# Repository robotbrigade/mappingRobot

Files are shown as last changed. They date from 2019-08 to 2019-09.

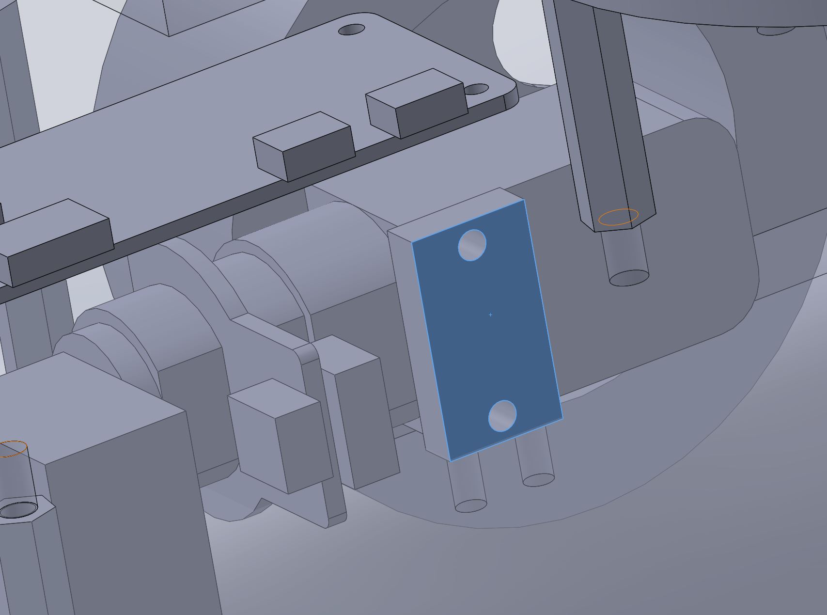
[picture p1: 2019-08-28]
CAD/Reference images/motor mount.jpg

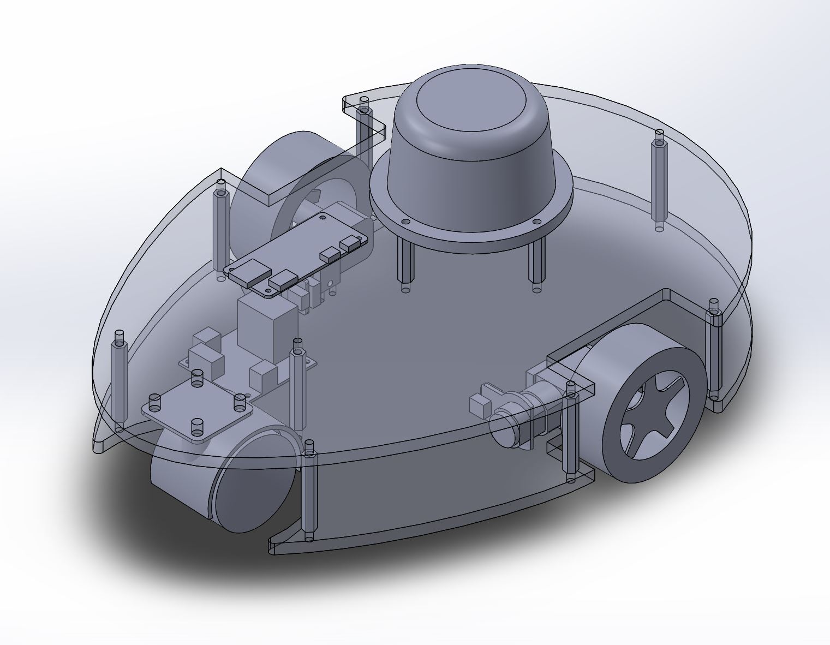
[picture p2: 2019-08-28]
CAD/Reference images/robot-with_transparency.jpg

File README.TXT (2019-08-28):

This readme was last updated on August 8th 2019

This repository will contain all of the files necessary to make a mapping robot that can map its 
environment using a 2D lidar-like sensor.  At the time of writing this README, the project is 
ongoing.  Eventual goals of this project are:

* Have the robot autonomously map its environment using a RPlidar A2 module.   
* Do so using ROS.  
* Run exclusively my own code.
* Be able to connect to the robot using a remote computer which can view the current stat of the
map as well as to take direct control of the robot.  

The robot system will consist of three processors.  The first is the remote computer which does no 
major computation.  The second is an onboard processor that will do the heavy lifting and which holds 
the most up-to-date map.  The third is a low-power processor (currently an arduino) that drives the 
motors, monitors the battery state, and turns on/off the power to the motors, the main processor, and
itself.  

Power is supplied to the robot from an off-the-shelf battery pack for a cordless drill.

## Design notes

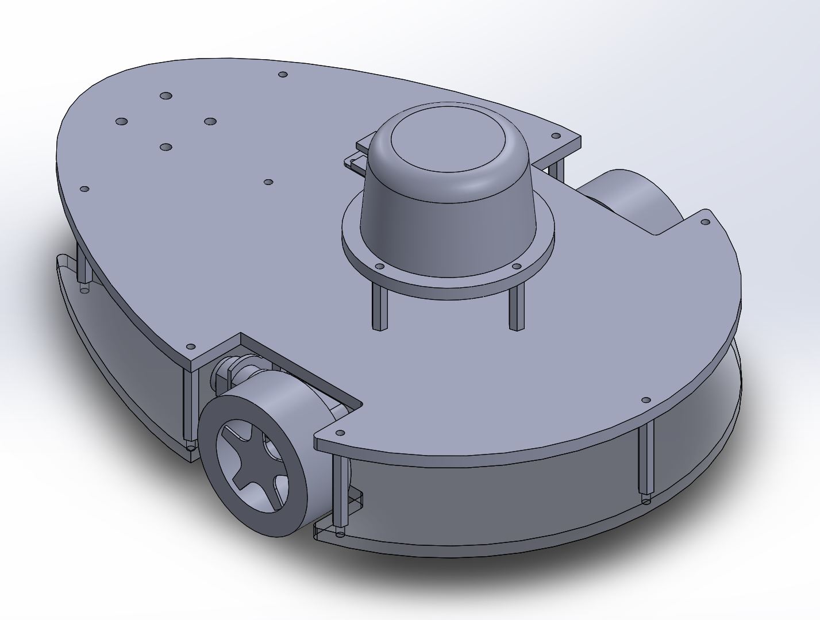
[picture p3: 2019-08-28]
CAD/Reference images/robot-everything_opaque.jpg

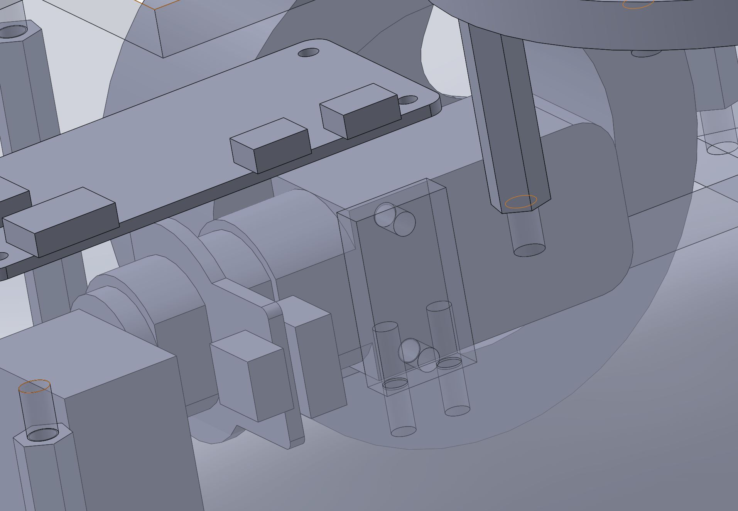
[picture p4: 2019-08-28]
CAD/Reference images/motor-mount-with-transparency.jpg

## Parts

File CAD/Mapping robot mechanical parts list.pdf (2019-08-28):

Quantity | Description | part number | Where to order | Alternate order location | Notes
2 Encoder/motor/gearbox combo | TT Motor with Encoder (6V 160RPM 120:1) | https://www.dfrobot.com/product-1457.html?search=TT%20Motor%20with%20Encoder%20%286V%20160RPM%20120%3A1%29
2 Wheels | https://www.dfrobot.com/product-352.html
1 1/4" black acrylic | https://www.amazon.com/gp/product/B01DYSTH3K
8 1 5/8" standoffs | https://www.mcmaster.com/91115A564
4 1" standoffs | https://www.mcmaster.com/91115A133
28 6-32 machine screws | https://www.mcmaster.com/92949A149
4 M3 machine screws | https://www.mcmaster.com/92000A120
4 6-32 lock nuts | https://www.mcmaster.com/91831A007
1 Caster | https://www.amazon.com/gp/product/B010SLSK48
2 motor mounts | https://www.pololu.com/product/2670https://www.robotshop.com/en/solarbotics-gmb39-gear-motor-bracket.html I scavenged my motor mounts from another project. Here are two mounts that I think would work but which aren't like the ones that I am using. You will need to adjust your CAD files to have the mounting holes be in the right places.
4 motor mount screws | Choose these to work with your motor mount
4 motor mount long machine screws | Choose these to work with your motor mount
4 motor mount lock nuts | Choose these to work with your motor mount

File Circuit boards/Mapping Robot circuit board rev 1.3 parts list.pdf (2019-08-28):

Qty | Value | Manufacturer part number | Where to order | Notes
1 | piece of wire put through the holes for the ground test point | ----
1 | Green LED | 754-1444-1-ND | Digikey
1 | Orange LED | 754-1156-1-ND | Digikey
1 | Red LED | 754-1153-1-ND | Digikey
1 | ARDUINO_Nano | Arduino nano | Ebay
1 | BEEPER | 433-1033-ND | Digikey
18 | 10 uF capacitor 1210 | 587-1818-1-ND | Digikey
6 | .1 uF CAPACITOR 1210 | 311-4522-1-ND | Digikey
1 | CONNECTOR_3_PIN - Servo | .1" header eg: HDR100IMP40M-G-V-TH-ND | Digikey
1 | CONNECTOR_3_PINMAYBE_JST-Got it from an assortment | 455-2248-ND | Digikey | I'm pretty sure that this is the right part number. I bought a bunch of these in an assortment
2 | CONNECTOR_4_PIN | 455-2249-ND | Digikey | I'm pretty sure that this is the right part number. I bought a bunch of these in an assortment
2 | CONNECTOR_6_PINJST_MAYBE -Got it from an assortment | 455-2271-ND | Digikey | I'm pretty sure that this is the right part number. I bought a bunch of these in an assortment
3 | DC_TO_DC_VARIABLE_555-1172-1-ND | 555-1172-1-ND | Digikey
1 | DIODESOD-23/SC-76 | BAT54HT1GOSCT-ND (https://www.digikey.com/product-detail/en/on-semiconductor/BAT54HT1G/BAT54HT1GOSCT-ND/917809) | Digikey
1 | FUSE_HOLDER_F065-ND36-4527-ND | F064-ND | Digikey
1 | HIGH-SIDE_SWITCH_INFINEON_ITS428L2 | ITS428L2ATMA1CT-ND (https://www.digikey.com/product-detail/en/infineon-technologies/ITS428L2ATMA1/ITS428L2ATMA1CT-ND/2231155) | Digikey
2 | MOSFET_N_CHANNELBSS138LCT-ND | BSS138LCT-ND | Digikey
10 | Fuses (2A) | F986-ND | Digikey
4 | Screw terminals for power / button | A113320-ND | Digikey
1 | Power button | Your choice since it isn't on the board! | Anywhere you want
5 | RESISTOR0805 - 10K | 311-10.0KCRCT-ND (https://www.digikey.com/product-detail/en/yageo/RC0805FR-0710KL/311-10.0KCRCT-ND/730482) | Digikey
1 | Resistor 0805 - 13.3K | 311-13.3KCRCT-ND | Digikey
1 | Resistor 0805 - 16.2K | 311-16.2KCRCT-ND | Digikey
1 | Resistor 0805 - 6.19K | 311-6.19KCRCT-ND | Digikey
1 | Resistor 0805 - 1K | 311-1.00KCRCT-ND | Digikey
1 | Resistor 0805 - 3.8K | 311-3.83KCRCT-ND (https://www.digikey.com/product-detail/en/yageo/RC0805FR-073K83L/311-3.83KCRCT-ND/730782) | Digikey
3 | Resistor 0808 - 220 Ohm | 311-220CRCT-ND | Digikey
1 | Resistor 0805 - 200K | 311-200KCRCT-ND | Digikey
1 | Resistor 0805 - 47K | 311-47.0KCRCT-ND | Digikey
1 | Resistor 0805 - 470 Ohm | 311-470CRCT-ND | Digikey
1 | Resistor 0805 - 1.2K | 311-1.20KCRCT-ND | Digikey
1 | Resistor 0805 - 590 Ohm | 311-590CRCT-ND | Digikey
3 | 680 pF 0805 capacitor | 478-10410-1-ND (https://www.digikey.com/product-detail/en/avx-corporation/08051A681FAT2A/478-10410-1-ND/6797579) | Digikey
1 | Battery holder | | https://www.thingiverse. com/thing:2996652 (https://www.thingiverse.com/thing:2996652)
1 | Circuit board

I ordered from allpcb.com but you could order from anywhere you want.

1 Raspberry Pi Zero W

https://www.adafruit.
com/product/3400 (https://www.adafruit.com/product/3400)

Note that I haven't completely decided on this one yet. It may not be powerful enough to do what I want in real-time

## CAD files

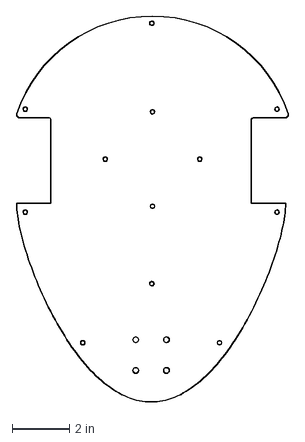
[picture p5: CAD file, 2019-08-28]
CAD/Use for laser cutting/upper chassis plate2_2.DXF
9.51 x 13.5 in

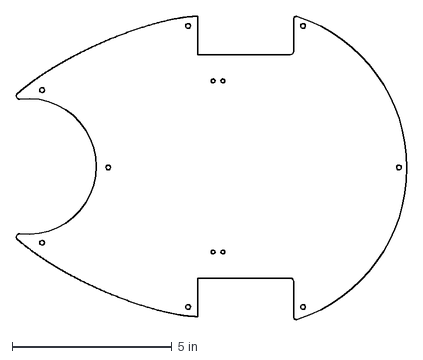
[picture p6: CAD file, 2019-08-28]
CAD/Use for laser cutting/lower chassis plate_2.DXF
12.2 x 9.51 in

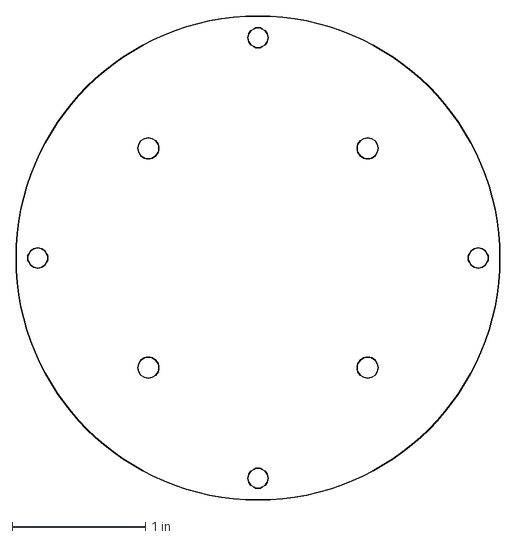
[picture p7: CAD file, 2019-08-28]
CAD/Use for laser cutting/rplidar mount_2.DXF
3.62 x 3.62 in

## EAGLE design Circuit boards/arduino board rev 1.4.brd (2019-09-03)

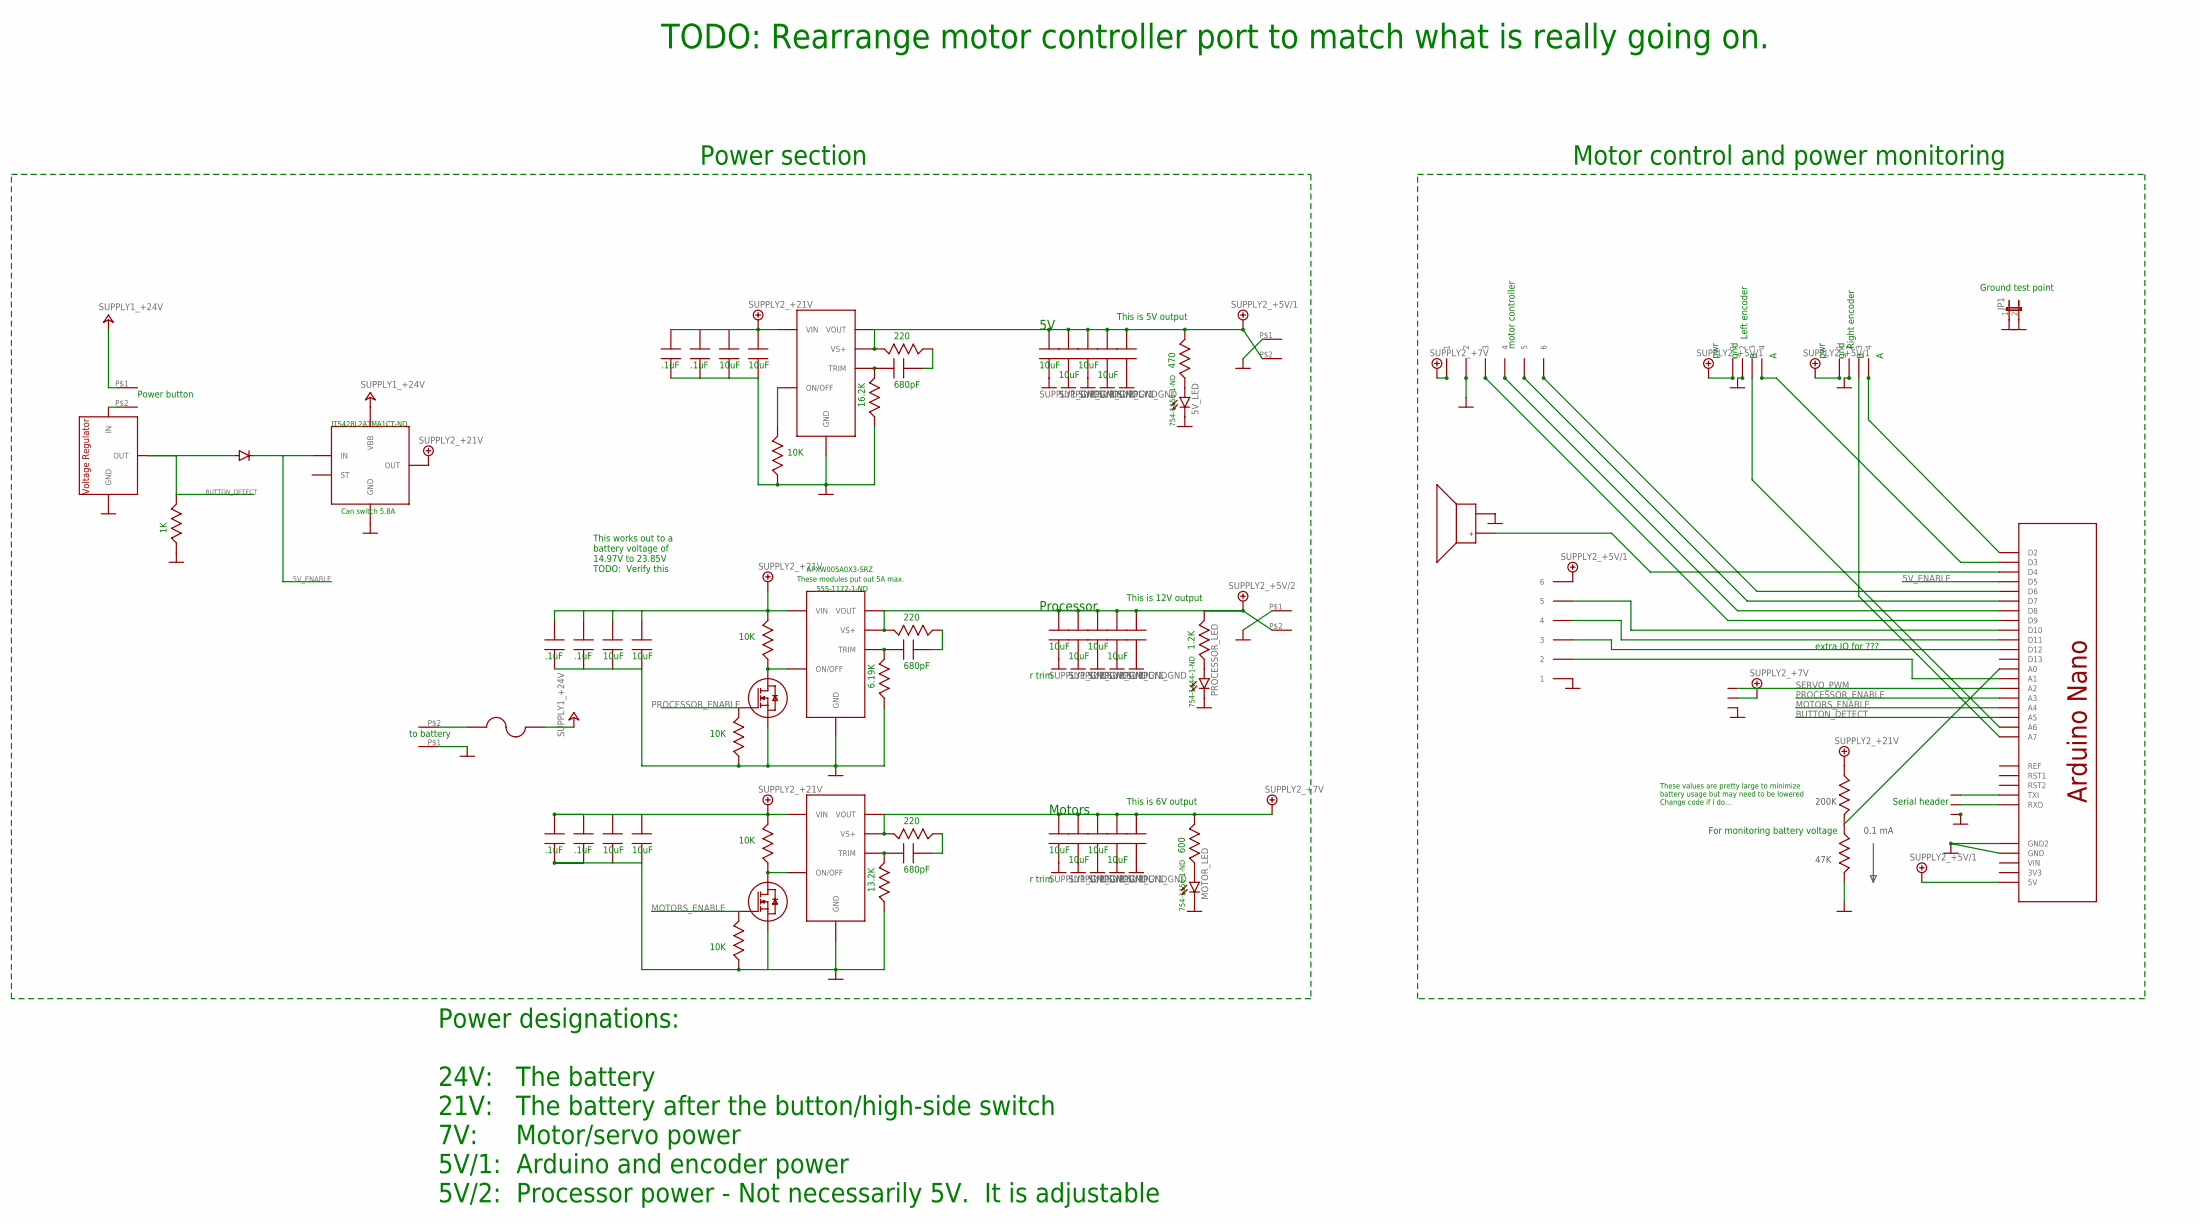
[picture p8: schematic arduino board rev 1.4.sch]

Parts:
5V_C_680PF: JACK_CAPACITOR0805; JACK_0805
5V_IN_CAP_1, 5V_IN_CAP_2, 5V_IN_CAP_3, 5V_IN_CAP_4, 5V_OUT_CAP_1, 5V_OUT_CAP_2, 5V_OUT_CAP_3, 5V_OUT_CAP_4, 5V_OUT_CAP_5: JACK_CAPACITOR; JACK_1210
5V_LED: LED_LEDSML1206; LED_SML1206
5V_LED_R1, 5V_REGULATOR_PULLDOWN, 5V_R_220: JACK_RESISTOR0805; JACK_0805
BATTERY_VOLTAGE_DIVIDER_HIGH: JACK_RESISTOR0805; JACK_0805
BATTERY_VOLTAGE_DIVIDER_LOW: JACK_RESISTOR0805; JACK_0805
BEEPER: JACK_BEEPER; JACK_BEEPER_433-1033-ND
DC2DC_PROCESSOR_: JACK_DC_TO_DC_VARIABLE_555-1172-1-ND; JACK_DC2DC_555-1172-1-ND
HIGH-SIDE_BLOCKING_DIODE: JACK_DIODESOD-23/SC-76; JACK_SOD-323/SC-76
HIGH-SIDE_SWITCH: JACK_HIGH-SIDE_SWITCH_INFINEON_ITS428L2; JACK_INFINEON_TO-252-5-11
HIGH-SIDE_SWITCH_BUTTON_DIVIDER_LOW: JACK_RESISTOR0805; JACK_0805
JP1: JUMPER_JP1E; JUMPER_JP1
MOTOR.1UF: JACK_CAPACITOR; JACK_1210
MOTOR_C_680PF: JACK_CAPACITOR0805; JACK_0805
MOTOR_ENABLE_MOSFET: JACK_MOSFET_N_CHANNELBSS138LCT-ND; JACK_SOT23
MOTOR_IN10UF, MOTOR_IN.1UF, MOTOR_IN.1UF1, MOTOR_IN.1UF4: JACK_CAPACITOR; JACK_1210
MOTOR_LED: LED_LEDSML1206; LED_SML1206
MOTOR_LED_R: JACK_RESISTOR0805; JACK_0805
MOTOR_MOSFET_PULLDOWN: JACK_RESISTOR0805; JACK_0805
MOTOR_PULLUP: JACK_RESISTOR0805; JACK_0805
MOTOR_R_220: JACK_RESISTOR0805; JACK_0805
MOTOR_TRIM: JACK_RESISTOR0805; JACK_0805
MOTOTR10UF, MOTOTR10UF1, MOTOTR10UF2, MOTOTR10UF3: JACK_CAPACITOR; JACK_1210
PROC10UF, PROC10UF1, PROC10UF2, PROC10UF3, PROC.1UF: JACK_CAPACITOR; JACK_1210
PROCESSOR_C_680PF: JACK_CAPACITOR0805; JACK_0805
PROCESSOR_ENABLE_MOSFET: JACK_MOSFET_N_CHANNELBSS138LCT-ND; JACK_SOT23
PROCESSOR_LED: LED_LEDSML1206; LED_SML1206
PROCESSOR_LED_R: JACK_RESISTOR0805; JACK_0805
PROCESSOR_MOSFET_PULLDOWN: JACK_RESISTOR0805; JACK_0805
PROCESSOR_PULLUP: JACK_RESISTOR0805; JACK_0805
PROCESSOR_R_220: JACK_RESISTOR0805; JACK_0805
PROC_IN10UF: JACK_CAPACITOR; JACK_1210
PROC_IN_.1UF, PROC_IN_.1UF1, PROC_IN_.1UF2: JACK_CAPACITOR; JACK_1210
RTRIM_5V: JACK_RESISTOR0805; JACK_0805
RTRIM_PROCESSOR: JACK_RESISTOR0805; JACK_0805
SERVO_HEADER: JACK_CONNECTOR_3_PIN; JACK_THREE_.1"_HOLES
U$1, U$2, U$5, U$6: JACK_SCREW_TERMINAL_2_CONDUCTORAMP-282837-2; JACK_AMP-282837-2
U$3, U$9: JACK_CONNECTOR_6_PINJST_MAYBE; JACK_JST_6_PIN_.1"
U$4, U$17: JACK_DC_TO_DC_VARIABLE_555-1172-1-ND; JACK_DC2DC_555-1172-1-ND
U$7: VOLTAGE_REGULATOR; JACK_SOT23
U$10, U$12: JACK_CONNECTOR_4_PIN; JACK_JST_4_PIN_.1"
U$11: JACK_FUSE_HOLDER_F065-ND; JACK_FUSE_HOLDER_F064-ND
U$13: JACK_CONNECTOR_3_PINMAYBE_JST; JACK_JST_3_PIN_.1"
U$14: JACK_ARDUINO_NANO

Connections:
5V_ENABLE: HIGH-SIDE_BLOCKING_DIODE.C, HIGH-SIDE_SWITCH.2 (IN), U$14.P$8 (D5)
+5V/1: 5V_LED_R1.P$3, 5V_OUT_CAP_1.2, 5V_OUT_CAP_2.2, 5V_OUT_CAP_3.2, 5V_OUT_CAP_4.2, 5V_OUT_CAP_5.2, 5V_R_220.P$3, U$2.P$2, U$3.6, U$4.VOUT, U$4.VS+, U$10.1, U$12.1, U$14.P$19 (5V)
+5V/2: DC2DC_PROCESSOR_.VOUT, DC2DC_PROCESSOR_.VS+, PROC10UF.2, PROC10UF1.2, PROC10UF2.2, PROC10UF3.2, PROC.1UF.2, PROCESSOR_LED_R.P$3, PROCESSOR_R_220.P$3, U$5.P$2
+7V: MOTOR.1UF.2, MOTOR_LED_R.P$3, MOTOR_R_220.P$3, MOTOTR10UF.2, MOTOTR10UF1.2, MOTOTR10UF2.2, MOTOTR10UF3.2, SERVO_HEADER.2, U$9.1, U$17.VOUT, U$17.VS+
+21V: 5V_IN_CAP_1.2, 5V_IN_CAP_2.2, 5V_IN_CAP_3.2, 5V_IN_CAP_4.2, BATTERY_VOLTAGE_DIVIDER_HIGH.P$2, DC2DC_PROCESSOR_.VIN, HIGH-SIDE_SWITCH.5 (OUT), MOTOR_IN10UF.2, MOTOR_IN.1UF.2, MOTOR_IN.1UF1.2, MOTOR_IN.1UF4.2, MOTOR_PULLUP.P$3, PROCESSOR_PULLUP.P$3, PROC_IN10UF.2, PROC_IN_.1UF.2, PROC_IN_.1UF1.2, PROC_IN_.1UF2.2, U$4.VIN, U$17.VIN
+24V: HIGH-SIDE_SWITCH.TAB (VBB), U$1.P$1, U$11.P$1
BUTTON_DETECT: HIGH-SIDE_BLOCKING_DIODE.A, HIGH-SIDE_SWITCH_BUTTON_DIVIDER_LOW.P$3, U$7.1 (OUT), U$14.P$22 (A5)
GND: 5V_IN_CAP_1.1, 5V_IN_CAP_2.1, 5V_IN_CAP_3.1, 5V_IN_CAP_4.1, 5V_LED.C, 5V_OUT_CAP_1.1, 5V_OUT_CAP_2.1, 5V_OUT_CAP_3.1, 5V_OUT_CAP_4.1, 5V_OUT_CAP_5.1, 5V_REGULATOR_PULLDOWN.P$2, BATTERY_VOLTAGE_DIVIDER_LOW.P$3, BEEPER.-, DC2DC_PROCESSOR_.GND, HIGH-SIDE_SWITCH.1 (GND), HIGH-SIDE_SWITCH_BUTTON_DIVIDER_LOW.P$2, JP1.1, JP1.2, MOTOR.1UF.1, MOTOR_ENABLE_MOSFET.2 (S), MOTOR_IN10UF.1, MOTOR_IN.1UF.1, MOTOR_IN.1UF1.1, MOTOR_IN.1UF4.1, MOTOR_LED.C, MOTOR_MOSFET_PULLDOWN.P$2, MOTOR_TRIM.P$2, MOTOTR10UF.1, MOTOTR10UF1.1, MOTOTR10UF2.1, MOTOTR10UF3.1, PROC10UF.1, PROC10UF1.1, PROC10UF2.1, PROC10UF3.1, PROC.1UF.1, PROCESSOR_ENABLE_MOSFET.2 (S), PROCESSOR_LED.C, PROCESSOR_MOSFET_PULLDOWN.P$2, PROC_IN10UF.1, PROC_IN_.1UF.1, PROC_IN_.1UF1.1, PROC_IN_.1UF2.1, RTRIM_5V.P$2, RTRIM_PROCESSOR.P$2, SERVO_HEADER.1, U$2.P$1, U$3.1, U$4.GND, U$5.P$1, U$6.P$1, U$7.3 (GND), U$9.2, U$10.2, U$12.2, U$13.1, U$14.P$12 (GND), U$14.P$17 (GND2), U$17.GND
IN: U$1.P$2, U$7.2 (IN)
MOTORS_ENABLE: MOTOR_ENABLE_MOSFET.1 (G), MOTOR_MOSFET_PULLDOWN.P$3, U$14.P$23 (A4)
unnamed: PROCESSOR_LED.A, PROCESSOR_LED_R.P$2
unnamed: MOTOR_LED.A, MOTOR_LED_R.P$2
unnamed: DC2DC_PROCESSOR_.ON/OFF, PROCESSOR_ENABLE_MOSFET.3 (D), PROCESSOR_PULLUP.P$2
unnamed: U$12.3, U$14.P$20 (A7)
unnamed: U$3.5, U$14.P$3 (D10)
unnamed: MOTOR_ENABLE_MOSFET.3 (D), MOTOR_PULLUP.P$2, U$17.ON/OFF
unnamed: U$9.6, U$14.P$7 (D6)
unnamed: U$12.4, U$14.P$11 (D2)
unnamed: U$6.P$2, U$11.P$2
unnamed: U$13.3, U$14.P$15 (TXI)
unnamed: U$13.2, U$14.P$14 (RXD)
unnamed: U$10.4, U$14.P$10 (D3)
unnamed: U$10.3, U$14.P$21 (A6)
unnamed: BEEPER.+, U$14.P$9 (D4)
unnamed: U$9.5, U$14.P$6 (D7)
unnamed: U$9.4, U$14.P$5 (D8)
unnamed: U$9.3, U$14.P$4 (D9)
unnamed: 5V_C_680PF.P$3 (2), RTRIM_5V.P$3, U$4.TRIM
unnamed: U$3.2, U$14.P$26 (A1)
unnamed: U$3.4, U$14.P$2 (D11)
unnamed: 5V_LED.A, 5V_LED_R1.P$2
unnamed: BATTERY_VOLTAGE_DIVIDER_HIGH.P$3, BATTERY_VOLTAGE_DIVIDER_LOW.P$2, U$14.P$27 (A0)
unnamed: U$3.3, U$14.P$1 (D12)
unnamed: 5V_REGULATOR_PULLDOWN.P$3, U$4.ON/OFF
unnamed: 5V_C_680PF.P$2 (1), 5V_R_220.P$2
unnamed: DC2DC_PROCESSOR_.TRIM, PROCESSOR_C_680PF.P$3 (2), RTRIM_PROCESSOR.P$3
unnamed: MOTOR_C_680PF.P$3 (2), MOTOR_TRIM.P$3, U$17.TRIM
unnamed: PROCESSOR_C_680PF.P$2 (1), PROCESSOR_R_220.P$2
unnamed: MOTOR_C_680PF.P$2 (1), MOTOR_R_220.P$2
PROCESSOR_ENABLE: PROCESSOR_ENABLE_MOSFET.1 (G), PROCESSOR_MOSFET_PULLDOWN.P$3, U$14.P$24 (A3)
SERVO_PWM: SERVO_HEADER.3, U$14.P$25 (A2)

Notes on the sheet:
to battery
Left encoder
Right encoder
motor controller
pwr
gnd
For monitoring battery voltage
extra IO for ???
r trim
Processor
Motors
Power section
Motor control and power monitoring
754-1156-1-ND
754-1444-1-ND
Ground test point
200K
47K
0.1 mA
Serial header
Power designations: 24V: The battery 21V: The battery after the button/high-side switch 7V: Motor/servo power 5V/1: Arduino and encoder power 5V/2: Processor power - Not necessarily 5V. It is adjustable
This works out to a battery voltage of 14.97V to 23.85V TODO: Verify this
These values are pretty large to minimize battery usage but may need to be lowered Change code if I do...
These modules put out 5A max.
555-1172-1-ND
APXW005A0X3-SRZ
ITS428L2ATMA1CT-ND
Can switch 5.8A
Power button
10K
This is 12V output
This is 6V output
This is 5V output
6.19K
13.2K
16.2K
220
680pF
10uF
.1uF

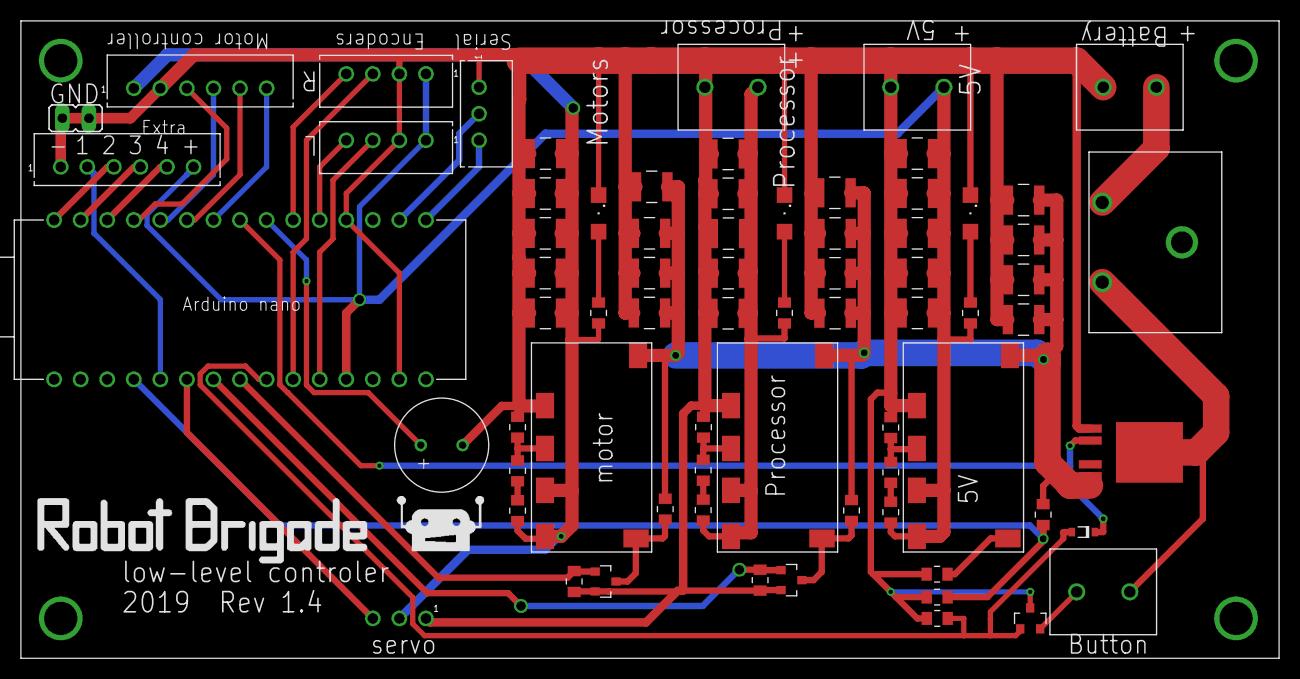
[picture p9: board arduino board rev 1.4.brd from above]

Board: 2 copper layers, 120.3 x 61.0 mm, 73 parts (0 on the bottom side), 41 nets.

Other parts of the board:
U$8: ROBOT_BRIGADE_LOGO_AND_TEXT_.2"

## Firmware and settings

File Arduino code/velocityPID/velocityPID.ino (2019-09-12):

/*   Firmware for Arduino board V4

     Written by Jack Buffington 2019 with the exception of the Morse Code beep functions, which are lightly modified from
     what can be found on the Arduino website.

     This board controls the motors and power for the mapping robot.  It is tasked with the following:
 *   * Drive according to commands given by the main processor
 *   * Control the power to the main processor, motors, and itself.
 *   * Monitor the battery voltage
 *   * Track position via encoders
 *   * Output beep or tone codes via a speaker
 *   * Determines if a wheel is stuck
 *   * Monitors bump sensors

     Control of this board will be done via serial data <TODO:  Verify that this is true.  It could be through USB serial.>

     This program will address serial commands through the main loop and will do the real-time tasks such as PID and reading
     the encoders from within interrupts.

     This program maintains a status byte which can be sent to the host processor.  The status byte is as follows:
     
    Status byte: <76543210>
    bit 7: in motion
    bit 6: left wheel stuck
    bit 5: right wheel stuck
    bit 4: bump sensor pressed
    bit 3: extra 4 is high
    bit 2: extra 3 is high
    bit 1: extra 2 is high
    bit 0: last motion completed successfully


    To program my Arduino clone, I need to select the processor as ATMEGA328P (Old Bootloader) otherwise I get a bunch of this:
    
    avrdude: stk500_recv(): programmer is not responding
    avrdude: stk500_getsync() attempt 1 of 10: not in sync: resp=0x00
    avrdude: stk500_recv(): programmer is not responding
    avrdude: stk500_getsync() attempt 2 of 10: not in sync: resp=0x00

     
     

*/

#define VOLTAGE_DETECT        A0
#define SERVO_PWM             A2
#define PROCESSOR_ENABLE      A3
#define MOTORS_ENABLE         A4
#define BUTTON                A5

#define MAIN_POWER_ENABLE     5
#define BEEPER                4

#define RIGHT_ENCODER_A       3
#define RIGHT_ENCODER_B       6
#define LEFT_ENCODER_A        2
#define LEFT_ENCODER_B        11


#define LEFT_MOTOR_PWM        10    // Pins 9 and 10 are capable of analog write.  The control scheme will need to take into account
#define LEFT_MOTOR_DIRECTION  7   // the direction and sometimes invert the PWM to match the actual desired speed.  The two pins 
#define RIGHT_MOTOR_DIRECTION 8    // for each motor correspond to the two outputs for the motor or in other words, the L298 is actually
#define RIGHT_MOTOR_PWM       9    // A quad half bridge device with the enables done in pairs.  


#define EXTRA_IO_4            A7   // A7 is analog input only!
#define EXTRA_IO_3            A6   // A6 is analog input only!
#define EXTRA_IO_2            12
#define EXTRA_IO_1            A1
#define LED                   13

// 14.97V is where my drill considers the battery to be dead
// After sitting for a while, a freshly charged battery is at 20.2V
#define BATTERY_FULL          20200
#define BATTERY_DEAD          15000

//#define SERIAL_BUFFER_SIZE    8
//// queue depth is how many messages can be waiting for the main program at any given time.
//#define QUEUE_DEPTH           3




//
// PID control values (yes, I did play with the values but this ended up working good enough...)
// You may want to play with them more if you need to make more rapid starts and stops to avoid oscillation.  
#define P_TERM                1 // 2       
#define D_TERM                1 // 3   






// for motor control
//unsigned int interruptsLeft = 0; // Used for determining how far to drive
int desiredLeftVelocity = 0;   // Used by the PID interrupt routine.  Don't write to these directly.  Let setupMotion() write to them.
int desiredRightVelocity = 0;


// For communicating with the PID interrupt
int rampingUpTimeslotsGlobal;
int rampingDownTimeslotsGlobal;
int constantTimeslotsGlobal;
int leftMaxVelocityGlobal;
int rightMaxVelocityGlobal;
int leftAccelerationGlobal;
int rightAccelerationGlobal;
volatile bool inMotion = false; // Volatile so that the compiler doesn't optimize away loops waiting for it to change.
 

// For keeping track of position
long leftEncoder;   // Actual position of the encoder
long rightEncoder; 
int  leftEncoderVelocity; // This is reset every interrupt and is used for PID calculations
int  rightEncoderVelocity;


void setup()
{
  // Enable power to the whole board without requiring that the user hold the button.  
  digitalWrite(MAIN_POWER_ENABLE, HIGH);

  // Wait a moment for power to stabilize then check the main battery voltage
  delay(100);

  // Set the pins to be inputs or outputs
  pinMode(VOLTAGE_DETECT, INPUT);
  pinMode(SERVO_PWM, OUTPUT);
  pinMode(PROCESSOR_ENABLE, OUTPUT);
  pinMode(MOTORS_ENABLE, OUTPUT);
  pinMode(BUTTON, INPUT);
  pinMode(MAIN_POWER_ENABLE, OUTPUT);
  pinMode(BEEPER, OUTPUT);
  pinMode(RIGHT_ENCODER_A, INPUT);
  pinMode(RIGHT_ENCODER_B, INPUT);
  pinMode(LEFT_ENCODER_A, INPUT);
  pinMode(LEFT_ENCODER_B, INPUT);
  pinMode(LEFT_MOTOR_PWM, OUTPUT);
  pinMode(LEFT_MOTOR_DIRECTION, OUTPUT);
  pinMode(RIGHT_MOTOR_PWM, OUTPUT);
  pinMode(RIGHT_MOTOR_DIRECTION, OUTPUT);
  pinMode(EXTRA_IO_4, OUTPUT);
  pinMode(EXTRA_IO_3, OUTPUT);
  pinMode(EXTRA_IO_2, OUTPUT);
  pinMode(EXTRA_IO_1, OUTPUT);
  pinMode(LED, OUTPUT);

  // Set up the USB serial port
  Serial.begin(2000000);

  beep(50,16000);
  beep(50,8000);
  beep(50,4000);
  beep(50,2000);
  beep(50,1000);
  beep(50,500);
  beep(50,250);
  beep(50,125);
  beep(50,62);

  setupMotorStuff();
} // end of setup()







void loop()
{  

  // Control the motors with ramping
  setupMotion(100, 300, 80, 8000);
  while(inMotion == true)
    { // Just hang out while the movement happens
    }
  Serial.println("A");


  
  setupMotion(-20, -300, 500, 3000);
  while(inMotion == true)
    { // Just hang out while the movement happens
    }
  Serial.println("B");
}










byte readBattery()
{ // outputs a value in the range of 0 to 100 which represents the roughly remaining capacity of the battery in percentage.ch tex
  

  /*
   *  Due to the voltage divider that I am using:  200K and 47K, this multiplies the voltage by .1903
   *  With 1024 counts for 5V, to get the voltage read, I need to multiply the counts by 5 and divide by 1024.
   *  To get the actual voltage of the battery, I would want to multiply that by 1/.1903.  To get this voltage, 
   *  it is roughly equivalent to multiplying by (1681/65536).  Of course, since we are dealing with only whole 
   *  numbers, this doesn't leave much resolution so this program is working in voltage * 1000.  This makes the 
   *  calculation be <analog reading> * (1681702/65536).  An unsigned long can handle the values in the range 
   *   0-4,294,967,295.  1681702 * 1024 (the max reading) is 1,722,062,848.  This will fit within an unsigned long!
   */
  unsigned long batteryVoltage;
  batteryVoltage = analogRead(VOLTAGE_DETECT); // gives me a value in the range of 0 to 1024.
  Serial.print("ADC reading: ");
  Serial.println(batteryVoltage);

  
  batteryVoltage *= 1681702;
  batteryVoltage >>= 16; // Make sure that the calculation is fast rather than doing a real division.
  Serial.print("voltage: ");
  Serial.println(batteryVoltage);
  
  

  // Calculate the rough remaining battery capacity based on a linear relationship to the voltage
  batteryVoltage -= BATTERY_DEAD;

  word batteryRange = BATTERY_FULL - BATTERY_DEAD;
  // Since I am working in integer math, I can't just divide batteryVoltage by the battery range since I
  // would get zero every time so I'm going to multiply the battery voltage by 100 first to give me a result in the range of
  // 0 to ~100.
  batteryVoltage *= 100;

  batteryVoltage /= batteryRange;

  if (batteryVoltage > 100) // It could be higher because I set the full voltage a little lower than what it really
    batteryVoltage = 100;   // is when it is full.

  return batteryVoltage;
}

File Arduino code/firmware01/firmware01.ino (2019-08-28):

/*   Firmware for Arduino board V3

     Written by Jack Buffington 2019 with the exception of the Morse Code beep functions, which are lightly modified from
     what can be found on the Arduino website.

     This board controls the motors and power for the mapping robot.  It is tasked with the following:
 *   * Drive according to commands given by the main processor
 *   * Control the power to the main processor, motors, and itself.
 *   * Monitor the battery voltage
 *   * Track position via encoders
 *   * Output beep or tone codes via a speaker
 *   * Determines if a wheel is stuck
 *   * Monitors bump sensors

     Control of this board will be done via serial data <TODO:  Verify that this is true.  It could be through USB serial.>

     This program will address serial commands through the main loop and will do the real-time tasks such as PID and reading
     the encoders from within interrupts.

     This program maintains a status byte which can be sent to the host processor.  The status byte is as follows:
     
    Status byte: <76543210>
    bit 7: in motion
    bit 6: left wheel stuck
    bit 5: right wheel stuck
    bit 4: bump sensor pressed
    bit 3: extra 4 is high
    bit 2: extra 3 is high
    bit 1: extra 2 is high
    bit 0: last motion completed successfully


    Currently using 5878 bytes of program space.  
     
     

*/

#define VOLTAGE_DETECT        A0
#define SERVO_PWM             A2
#define PROCESSOR_ENABLE      A3
#define MOTORS_ENABLE         A4
#define BUTTON                A5
#define FIVE_VOLT_ENABLE      A6
#define BEEPER                A7
#define RIGHT_ENCODER_A       2
#define RIGHT_ENCODER_B       4
#define LEFT_ENCODER_A        3
#define LEFT_ENCODER_B        5

#define MOTOR_CONTROLLER_6    6
#define MOTOR_CONTROLLER_5    7
#define MOTOR_CONTROLLER_4    8
#define MOTOR_CONTROLLER_3    9

#define LEFT_MOTOR_PWM        6   // TODO: THESE PINS ARE JUST A GUESS!  Figure out what they really are and fix this.
#define LEFT_MOTOR_DIRECTION  7
#define RIGHT_MOTOR_PWM       8
#define RIGHT_MOTOR_DIRECTION 9


#define EXTRA_IO_4            10
#define EXTRA_IO_3            11
#define EXTRA_IO_2            12
#define EXTRA_IO_1            A1
#define LED                   13

// 14.97V is where my drill considers the battery to be dead
// It reads 23.85V when full.
#define BATTERY_FULL          23500
#define BATTERY_DEAD          15000

#define SERIAL_BUFFER_SIZE    8
// queue depth is how many messages can be waiting for the main program at any given time.
#define QUEUE_DEPTH           3

#define TICKS_PER_METER       10000   // TODO:   Figure out the correct value for this (1920 pulses per wheel revolution)

// How many times per second the PID interrupt happens per second.
#define PID_INTERRUPT_RATE    10
#define P_TERM                32   
#define I_TERM                0
#define D_TERM                0
#define PID_SHIFT_POSITIONS   6     // effectively divide the PID terms by 64


#define DOT_DELAY            200 // for morse code

#define MAX_USER_MESSAGE_LENGTH   100



char* letters[] = {
  ".-", "-...", "-.-.", "-..", ".", "..-.", "--.", "....", "..", // A-I
  ".---", "-.-", ".-..", "--", "-.", "---", ".--.", "--.-", ".-.", // J-R
  "...", "-", "..-", "...-", ".--", "-..-", "-.--", "--.." // S-Z
};

char* numbers[] = {
  "-----", ".----", "..---", "...--", "....-", ".....",
  "-....", "--...", "---..", "----."
};



byte serialBuffer[SERIAL_BUFFER_SIZE];
byte messageQueue[QUEUE_DEPTH][SERIAL_BUFFER_SIZE - 1];
byte messagesInQueue = 0;
byte userMessage[MAX_USER_MESSAGE_LENGTH];

// for motor control
int leftMotorTicksPerInterrupt = 0;
int rightMotorTicksPerInterrupt = 0;
unsigned int remainingInterruptsToDriveMotors = 0;

// For keeping track of position
long leftEncoder; 
long rightEncoder;
long lastLeftEncoder; // since it was last checked via serial command
long lastRightEncoder;

byte statusByte;  // for sending status messages

bool thereIsAnUserMessage;
byte userMessageSize;
byte currentUserMessageCharacter;



void setup()
{
  // Enable power to the Arduino
  digitalWrite(FIVE_VOLT_ENABLE, HIGH);

  // Wait a moment for power to stabilize then check the main battery voltage
  delay(100);
  int batteryPercent = readBattery();
  //if (batteryPercent > 10)    //    TODO:   UNCOMMENT THIS LINE FOR PRODUCTION CODE
  {
    // Set the pins to be inputs or outputs
    pinMode(VOLTAGE_DETECT, INPUT);
    pinMode(SERVO_PWM, OUTPUT);
    pinMode(PROCESSOR_ENABLE, OUTPUT);
    pinMode(MOTORS_ENABLE, OUTPUT);
    pinMode(BUTTON, INPUT);
    pinMode(FIVE_VOLT_ENABLE, OUTPUT);
    pinMode(BEEPER, OUTPUT);
    pinMode(RIGHT_ENCODER_A, INPUT);
    pinMode(RIGHT_ENCODER_B, INPUT);
    pinMode(LEFT_ENCODER_A, INPUT);
    pinMode(LEFT_ENCODER_B, INPUT);
    pinMode(MOTOR_CONTROLLER_6, OUTPUT);
    pinMode(MOTOR_CONTROLLER_5, OUTPUT);
    pinMode(MOTOR_CONTROLLER_4, OUTPUT);
    pinMode(MOTOR_CONTROLLER_3, OUTPUT);
    pinMode(EXTRA_IO_4, OUTPUT);
    pinMode(EXTRA_IO_3, OUTPUT);
    pinMode(EXTRA_IO_2, OUTPUT);
    pinMode(EXTRA_IO_1, OUTPUT);

    // NOTE:  Output pins are automatically LOW when first set to output unless they were previously set to HIGH.

    statusByte = 1;

    // Give the user an idea of the battery voltage in the range of 1 to 10
    batteryPercent /= 10;
    char percentChar[] = {batteryPercent + 48, 0};  // 48 shifts it into the correct ascii character range
    sendMorseString(percentChar);

    // Enable the main processor
    digitalWrite(PROCESSOR_ENABLE, HIGH);

    Serial1.begin(115200);


    // Set up the encoder interrupts
    // By default the external interrupts have higher priority than timer interrupts.  That is what I want.
    attachInterrupt(digitalPinToInterrupt(LEFT_ENCODER_A), leftEncoderInterrupt, CHANGE);
    attachInterrupt(digitalPinToInterrupt(RIGHT_ENCODER_A), rightEncoderInterrupt, CHANGE);
   

    // Set up the PID interrupt
    leftEncoder = 0;
    rightEncoder = 0;
    lastLeftEncoder = 0; 
    lastRightEncoder = 0;


    thereIsAnUserMessage = false;

  }
  else
  { // The battery is too low to operate the robot so shut down.
    // disable power to the Arduino
    digitalWrite(FIVE_VOLT_ENABLE, LOW);
    while (1)
    { // hang out here while the power dies.

    }
  }


}
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

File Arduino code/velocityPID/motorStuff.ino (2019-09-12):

// Things in this file relate to driving the motors.  


void setupMotorStuff()
{
  // Set up the encoder interrupts
  // By default the external interrupts have higher priority than timer interrupts.  That is what I want.
  attachInterrupt(digitalPinToInterrupt(LEFT_ENCODER_A), leftEncoderInterrupt, CHANGE);
  attachInterrupt(digitalPinToInterrupt(RIGHT_ENCODER_A), rightEncoderInterrupt, CHANGE);

  // Set up the PID interrupt
  leftEncoder = 0;
  rightEncoder = 0;

  
  // A good reference for timer interrupt code is: http://www.8bit-era.cz/arduino-timer-interrupts-calculator.html
  // The Arduino codebase already has timer0 set up so that an interrupt (or something) happens every 1/1000th of 
  // a second so I'm just enabling my own interrupt here.  
  
  // enable timer compare interrupt
  TIMSK0 |= (1 << OCIE0A);
}



void driveLeftMotor(bool forward, int speed)
{// Drives the left motor in the direction specified relative to the robot
 // The speed is adjusted upward because the motors on this robot don't start moving until about a value of 35.
 // They stop moving at a value of about 32.
 //  Don't use this function directly.  It is called by the timer0 ISR.
  
  
  // adjust the speed and then limit to 255
  if(speed != 0) // Allow it to truly stop
    speed += 35;
    
  if(speed > 255)
    speed = 255;
  
  if(forward)
  {
    digitalWrite(LEFT_MOTOR_DIRECTION,LOW);
    analogWrite(LEFT_MOTOR_PWM,speed);
  }
  else
  {
    digitalWrite(LEFT_MOTOR_DIRECTION,HIGH);
    analogWrite(LEFT_MOTOR_PWM,255-speed);
  }
}

long readLeftEncoder()
{ // Use this function if you need to read from the encoder since it is multiple bytes and could be corrupted by an interrupt
  // happening during the read
  noInterrupts();
  long temp = leftEncoder;
  interrupts();
  return temp;
}

long readRightEncoder()
{ // Use this function if you need to read from the encoder since it is multiple bytes and could be corrupted by an interrupt
  // happening during the read
  noInterrupts();
  long temp = rightEncoder;
  interrupts();
  return temp;
}



void driveRightMotor(bool forward, int speed)
{// Drives the right motor in the direction specified relative to the robot
 // The speed is adjusted upward because the motors on this robot don't start moving until about a value of 35.
 // They stop moving at a value of about 32.
 //  Don't use this function directly.  It is called by the timer0 ISR.

  // adjust the speed and then limit to 255
  if(speed != 0) // Allow it to truly stop
    speed += 35;
  if(speed > 255)
    speed = 255;
    
  if(forward)
  {
    digitalWrite(RIGHT_MOTOR_DIRECTION,HIGH);
    analogWrite(RIGHT_MOTOR_PWM,255-speed);
  }
  else
  {
    digitalWrite(RIGHT_MOTOR_DIRECTION,LOW);
    analogWrite(RIGHT_MOTOR_PWM,speed);
  }
}




void leftEncoderInterrupt()
{ /*  This interrupt happens when the A input of the left encoder changes. 
      I'm not sure how to look at the assembly code generated by an Arduino sketch so I'm basing my timing information 
      on information from http://www.gammon.com.au/interrupts
      It is saying that using attachInterrupt() It takes 5.125 uS to just jump into and out of an interrupt.  That gives an interrupt
      rate of 195,121 interrupts per second if nothing is done. Divide that by two encoders and I get 97560 interrupts per second per encoder.
      Given that my encoders are 16 pulses per revolution and the gearbox is 120:1 I should have 1920 pulses per wheel revolution.  The motor has a 
      no-load RPM of 160 at 6V.  This works out to 2.667 revolutions per second.  This gives a maximum pulse rate of 5120 pulses per second.  This is 
      well within the maximum so I won't bother to optimize to make this routine faster.
  */  
  bool A = digitalRead(LEFT_ENCODER_A);
  bool B = digitalRead(LEFT_ENCODER_B);

  if(A)
  {
    if(B)
    {
      leftEncoder++;
      leftEncoderVelocity++;
    }
    else
    {
      leftEncoder--;
      leftEncoderVelocity--;   
    }
  }
  else
  {
    if(B)
    {
      leftEncoder--;
      leftEncoderVelocity--;
    }
    else
    { 
      leftEncoder++;
      leftEncoderVelocity++;
    }
  }
}



void rightEncoderInterrupt()
{ /*  This interrupt happens when the A input of the left encoder changes. 
  */  
  bool A = digitalRead(RIGHT_ENCODER_A);
  bool B = digitalRead(RIGHT_ENCODER_B);

  if(A)
  {
    if(B)
    {
      rightEncoder++;
      rightEncoderVelocity++;
    }
    else
    {
      rightEncoder--;   
      rightEncoderVelocity--;
    }
  }
  else
  {
    if(B)
    {
      rightEncoder--;
      rightEncoderVelocity--;
    }
    else
    {
      rightEncoder++;
      rightEncoderVelocity++;
    }
  }
}
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

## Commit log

2019-08-28 Added cad files and DXF files used for laser cutting
    [lower chassis plate_2.DXF, rplidar mount_2.DXF, upper chassis plate2_2.DXF]
2019-09-03 Updated board test code and fixed circuit board's power-up issue
    [arduino board rev 1.4.brd, arduino board rev 1.4.sch]
2019-09-04 Updated the boardtest file
2019-09-08 PID nearly tuned for position mode
2019-09-09 Velocity PID is tuned pretty well
2019-09-10 velocity PID is working now with no ramping
2019-09-12 Motor control is fully working now
